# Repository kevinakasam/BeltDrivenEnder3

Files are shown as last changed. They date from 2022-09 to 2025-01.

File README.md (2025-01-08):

# BeltDrivenEnder3

### Versions/Variants
1: Stock V-Wheels        |  2: MGN-12H   |  3: Dual Z (Wheels and MGN)
:-------------------------:|:-------------------------:|:-------------------------:
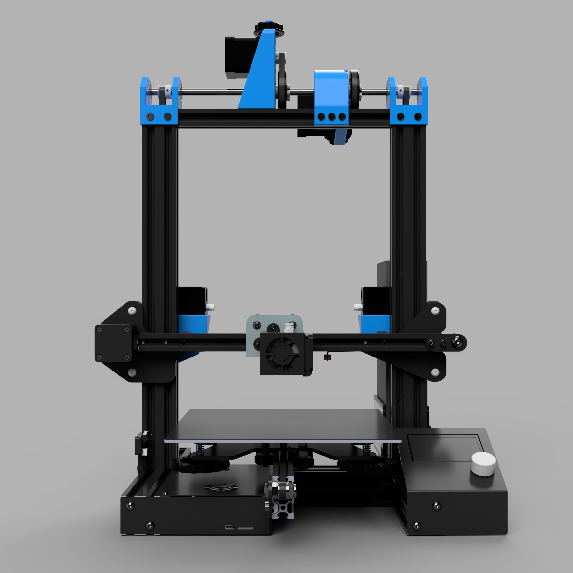
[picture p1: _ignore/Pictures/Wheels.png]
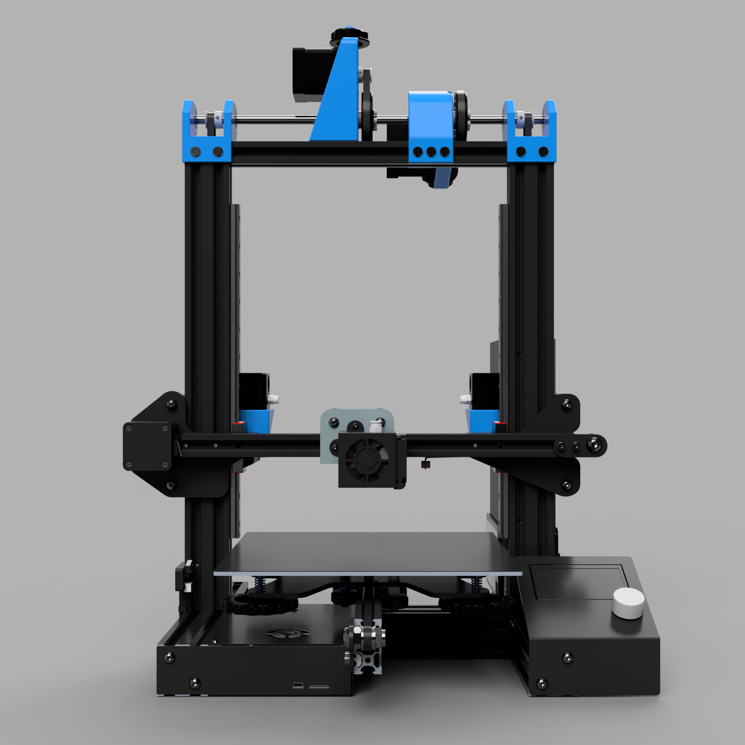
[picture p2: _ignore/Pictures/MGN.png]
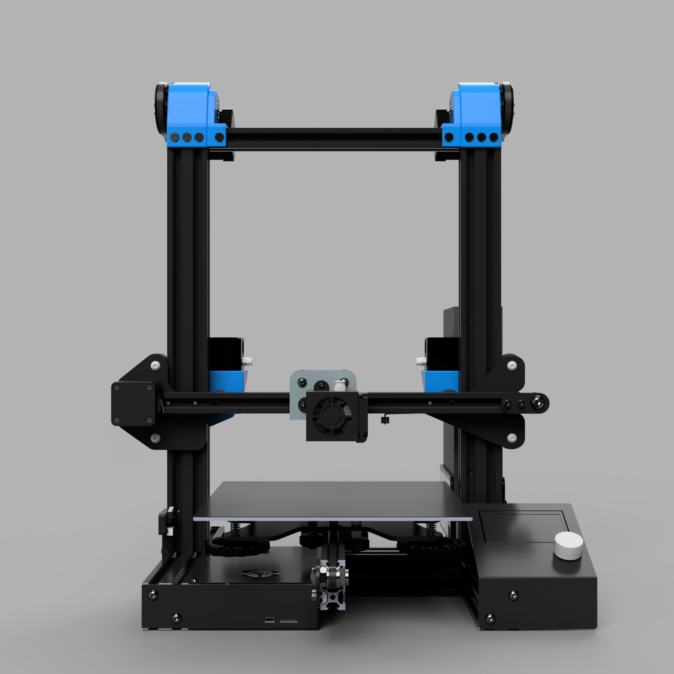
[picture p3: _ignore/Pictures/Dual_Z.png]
  |   |  

---
## Hello and welcome to the Belt Driven Z Mod.
### STLs, Bill of Materials and Instructions 
Please visit my [website](https://www.kevinakasam.com/belt-driven-ender-3/) to start the Config Finder. I have spent many hours creating a very interactive and easy to follow guide for the mod. You will get all the files you need at the end of the Config Finder, including a zip file with all the STLs, materials you need, and the instructions for your particular setup.

<a href="https://kevinakasam.com/belt-driven-ender-3/">
         Click
      </a>

### ❤️ Support my work

All my work is 100% Open-Source and free for everyone to use. But designing and developing all these mods takes a lot of time and effort, so if you appreciate my work and would like to support it and also help cover the costs of gettings the mods perfect, you can use one of the following links. Thanks a lot 🤍

<a href="https://www.buymeacoffee.com/kevinakasam" target="_blank">Buy Me A Coffee</a>


### Further notes
#### Versions vs. Variants
This mod now exists in the 3rd version (V3). The _ignore folder contains all the files for the old versions (V1 and V2). The current version (V3) exists in 3 variations:V-Wheels, MGN-12h and Dual Z (Dual Z works with both variants V-Wheels and MGN-12h). In addition, you can choose between the normal and ultralow version. I hope this clarifies the confusion between the versions and variants. Again please use the config finder on my [website](https://www.kevinakasam.com/belt-driven-ender-3/) to configure your individual setup.

#### Attention!
I'm not an expert and 3D printing is my hobby. So please be careful when you rebuild this mod and don't just go ahead. For my printer the parts fit perfectly.
Everybody bears the risks of a modification himself.
All parts can be modified as you like. :D

#### Print settings
All Parts can be printed without support. Keep the orientation for best results. Yes, you can use PLA but no, you shouldn’t use PLA. I used PETG for the unenclosured, ABS for the enclosured printer. Suggested print settings: 50% Infill, 5 Walls/Top-Bottom layer.
Good luck and happy printing!

#### Why I made the Mod:
My Ender 3 always had problems with the Z-axis, which were caused by a bent and misaligned leadscrew. Therefore I decided to convert the Ender to belts in Z as well.
This mod also solves the problem of a hanging x-axis on the right side. Because of the two belts, both sides run synchronously and can also be adjusted very precisely.

#### What this Mod can't do:
This mod can't solve problems that are caused by an inconsitent extrusion. Inconsitent extrusion means an untuned Flowrate/Extrusion multiplier and causes very inconsitent layers --> this looks like the picture below. To get rid of that you should tune all extrusion related values, like Flowrate an Linear Advance (Marlin) / Pressure Advance (Klipper). Take a look at this [tuning guide](https://ellis3dp.com/Print-Tuning-Guide/), its very well made (Works also for non Voron Printers and Marlin machines). 

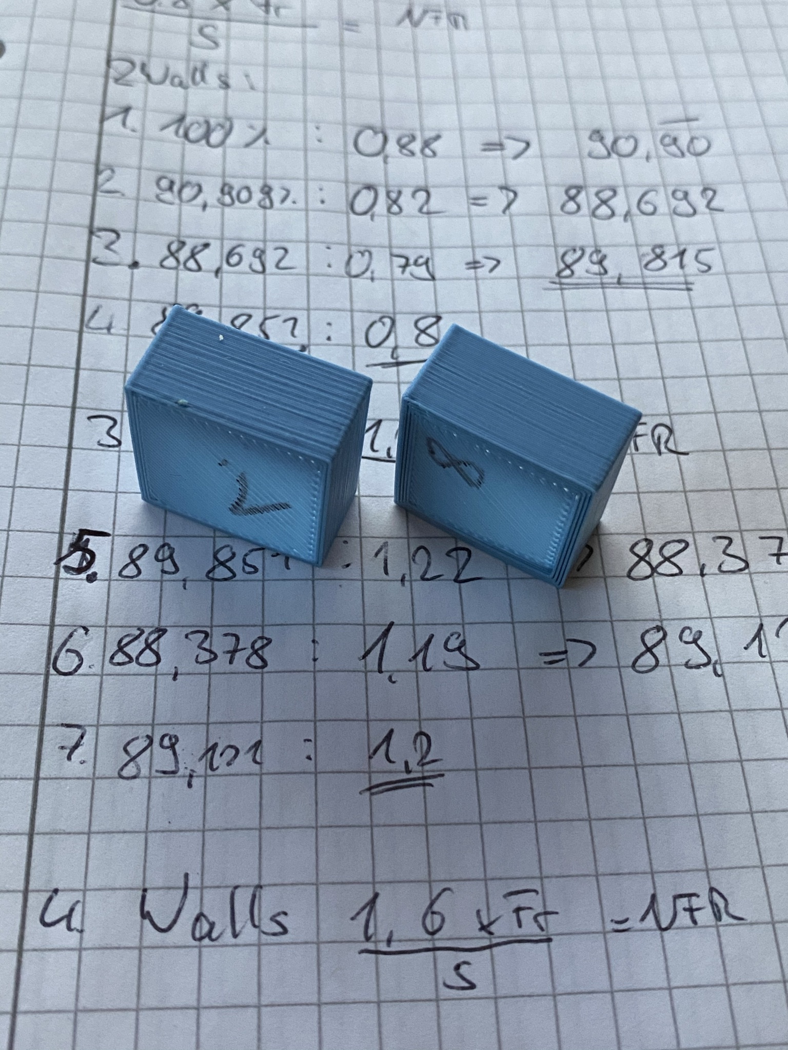
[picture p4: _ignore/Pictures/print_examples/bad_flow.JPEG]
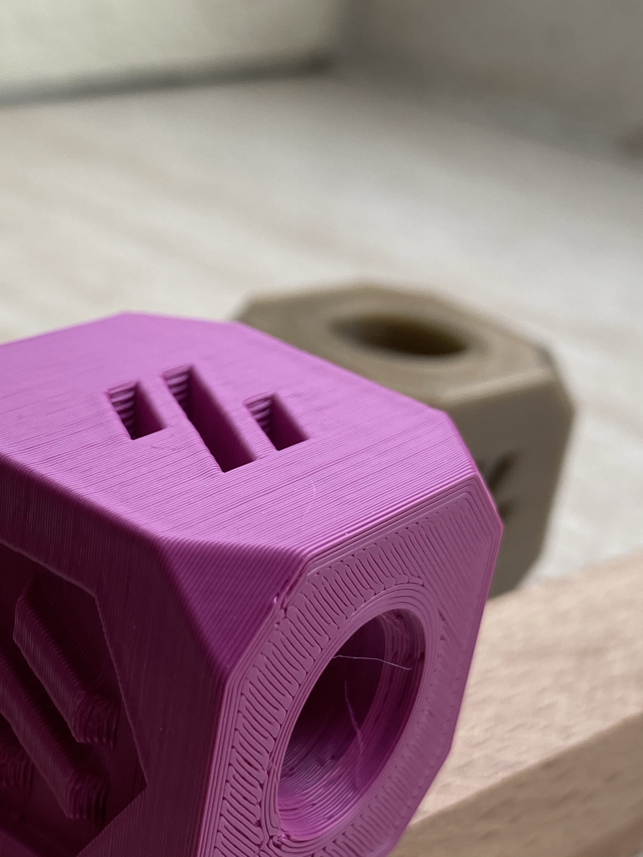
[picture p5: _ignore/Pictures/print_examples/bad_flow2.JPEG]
 

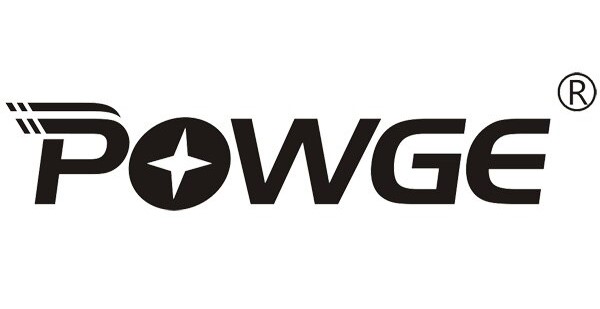
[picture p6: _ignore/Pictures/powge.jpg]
####  Powered by Powge! 
I am very very proud to announce that there is now a Motion Kit for this mod available for purchase! The Motion Kit from Powge provides all parts for Single Z or Dual Z, with F623 or 20T Idlers and in black or silver. This allows us to use high quality parts at a low price! Belts and pulleys match up perfectly and make the mod a little better. Thanks to Powge for this opportunity! (btw Aliexpress shows delivery times of several months, but shipping is significantly faster (to Germany it takes about 10 days)).
Link to the kit (also included in the BOM): https://www.aliexpress.com/item/1005003933709487.html

#### A word about *linear rails*.
There's a reason I haven't made a rail version in a very long time: Rails are not better than rollers in ***terms of quality***. At least the cheap rails you can buy on AliExpress. The tolerances are not good, they don't last long and can give z artifacts that you don't have with rollers. From time to time I get messages that the x axis drops as soon as the power is turned off. Every time that happens the mod uses rails. And like almost of those has cheap china rails. The problem with these cheap rails is that there is no friction at all, no tension and the Z axis is very poorly guided. The little Z motor has to carry all the weight because the rails are so loose they can't take any load. 
You also have to take care of the rails, lubricate and clean them from time to time, and make sure they don't leak. So you will spend a lot of money on a set of rails if you want good rails. Plus lubricants, cleaners, etc. Also, mounting the rails is more complicated. With wheels, you spent almost nothing on a new wheel, put it on, and you are good to go.
So I recommend trying wheels first and if you still want rails, you just need to print two small adapters to install the rails. Keep things simple ;)
  
#### How to use the toothed idlers
You have to remove the flage of the toothed idlers, otherwise they would get in contact with the profile.



### Acknowledgements
I would like to thank everyone who supported this project, especially *Guffy* and the *Awesome Helpers* from my Discord! 
Also a big thank you to my mate Deutherius who helped me with the initial setup of this mod!

#### Thank you Voron
This mod uses a modified transmission from the Voron 2.2. I made a different frame to mount it on the Ender 3. The tensionerarm and the tensionerring are from the Voron guys. These aren’t my work!!! The mount and the 80T gear are made by myself. Because the parts will be updated regularly, you can find the STLs I used on GitHub 

#### THANK YOU VERY MUCH!
I want to thank everyone who has helped me over the last months with feedback, support and confidence. Without you this mod would not have become sich a thing! Thanks also to Creality for the Golbal DIY Contest. I am very proud to announce that I could reach the 3rd place with his mod.

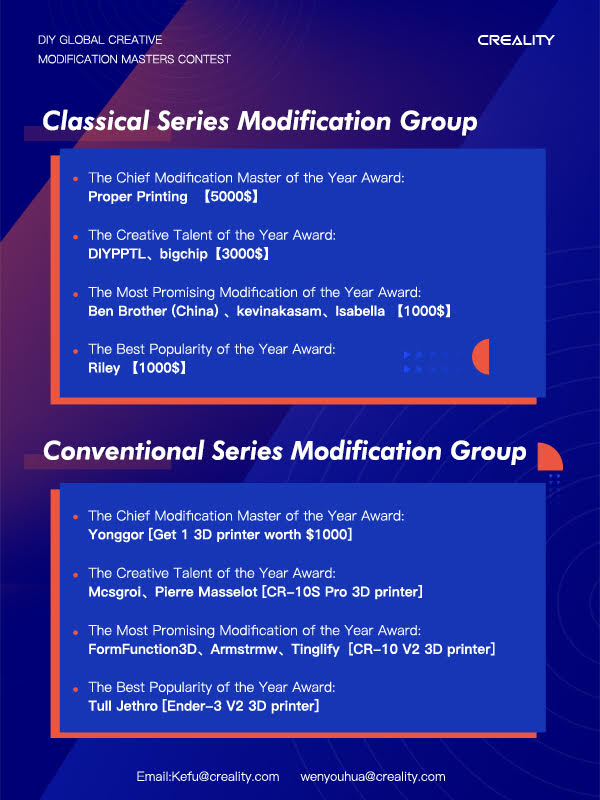
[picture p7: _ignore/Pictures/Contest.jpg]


## Print Showcase
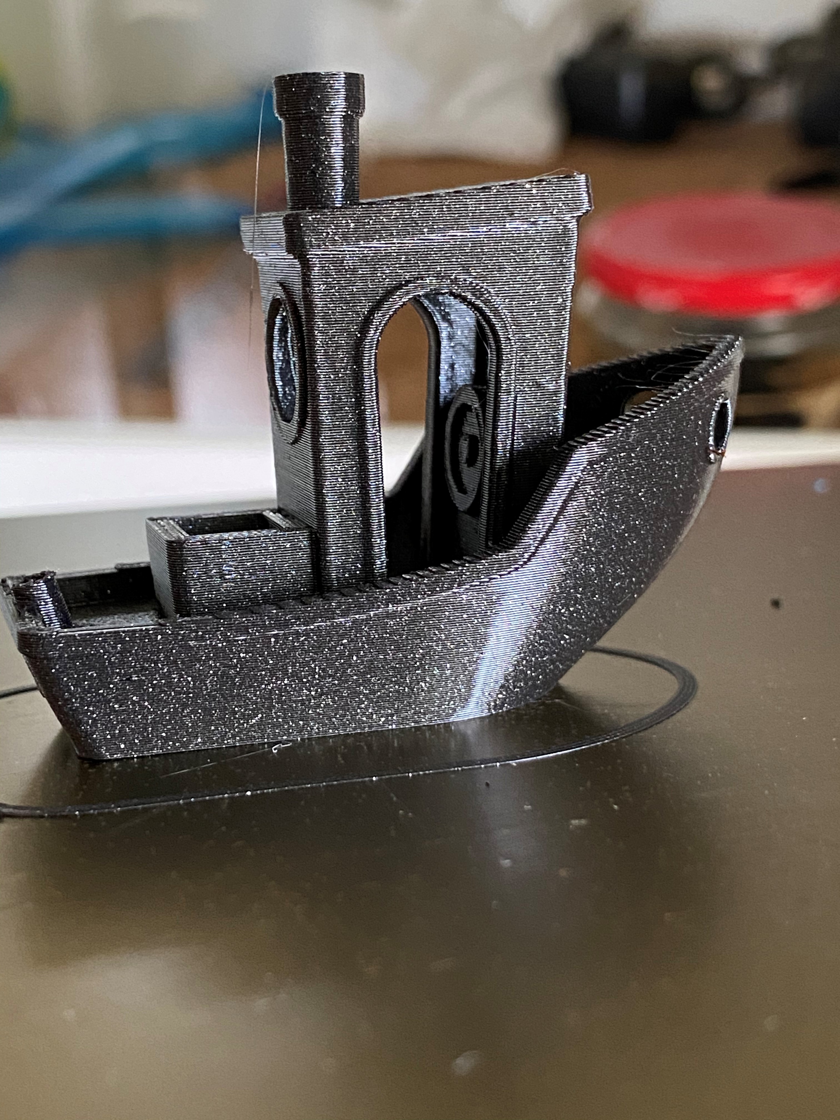
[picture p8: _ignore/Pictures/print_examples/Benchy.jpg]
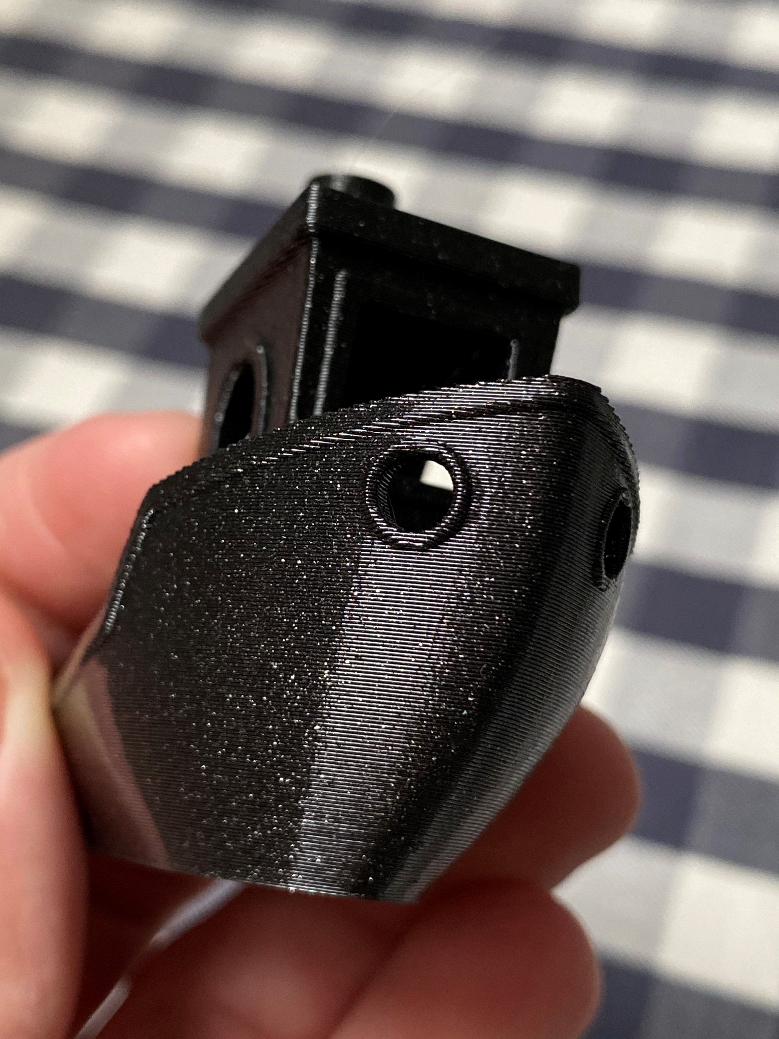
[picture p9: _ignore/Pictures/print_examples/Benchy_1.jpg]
 
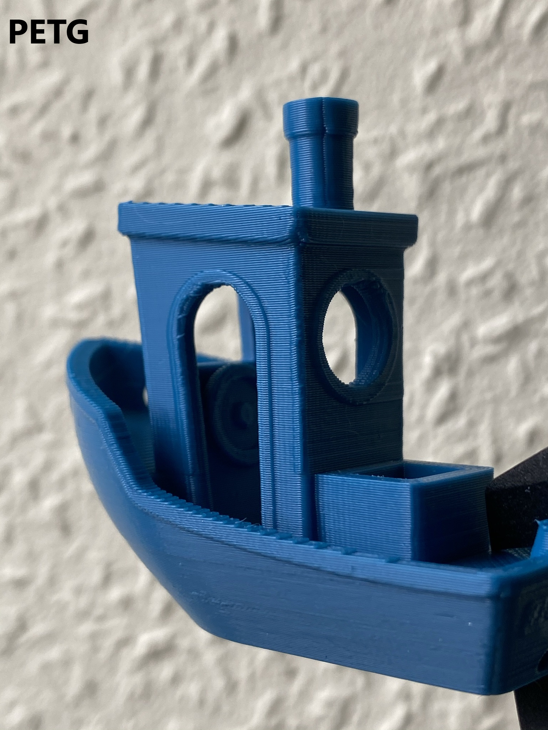
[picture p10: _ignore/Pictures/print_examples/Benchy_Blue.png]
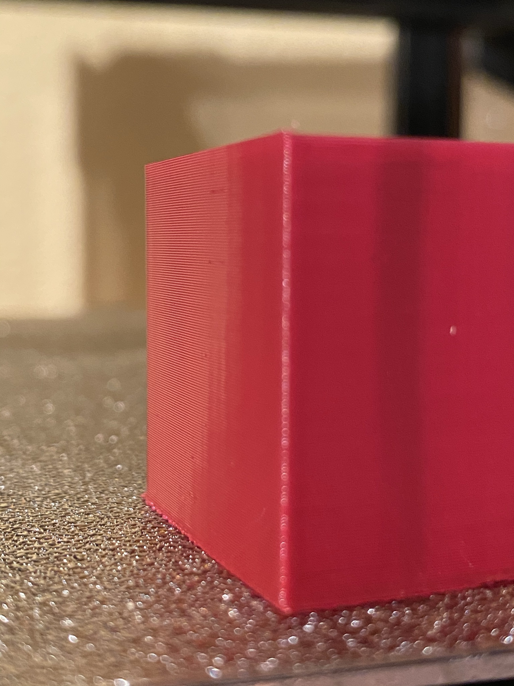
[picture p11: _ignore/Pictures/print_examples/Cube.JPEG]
 
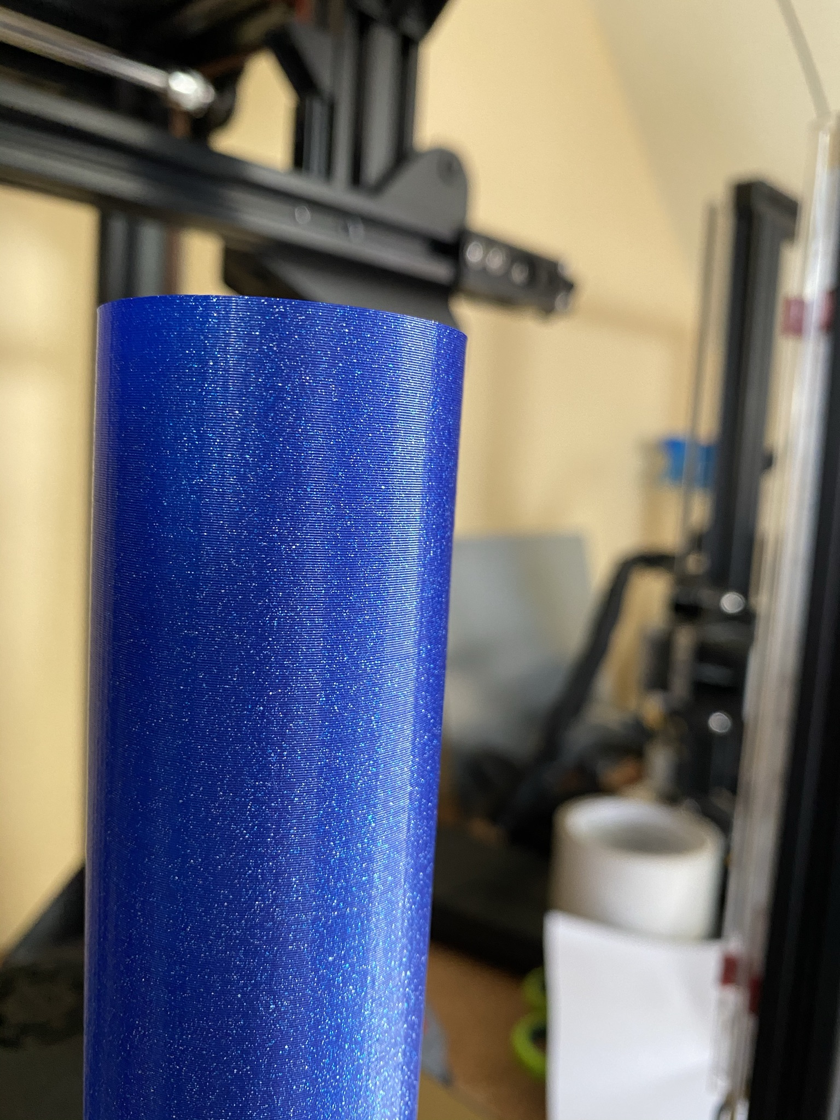
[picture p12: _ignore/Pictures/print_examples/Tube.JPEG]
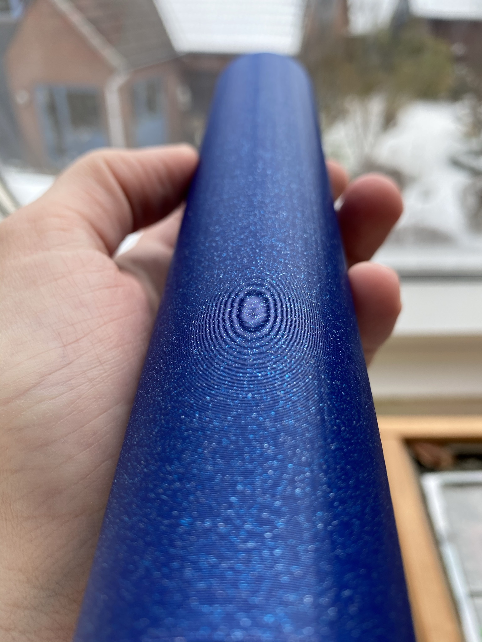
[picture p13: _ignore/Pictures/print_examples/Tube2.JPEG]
 

## Finally the video tutorials are finished!
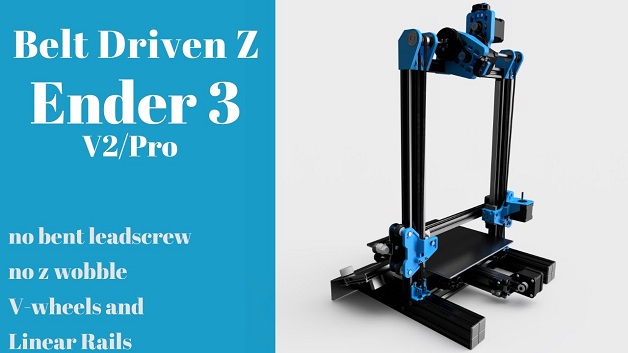
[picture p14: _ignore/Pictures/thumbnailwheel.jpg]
Video Tutorial (https://youtu.be/oUdoJUs8Zcg)


https://youtu.be/oUdoJUs8Zcg

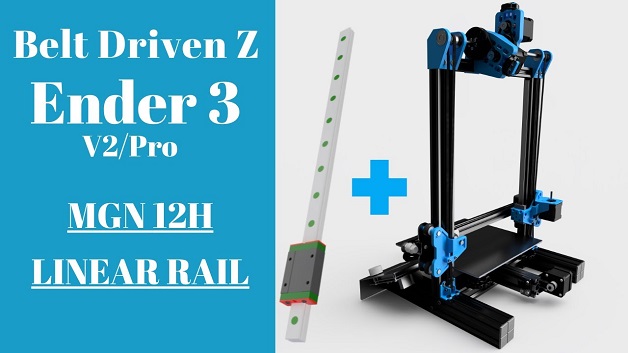
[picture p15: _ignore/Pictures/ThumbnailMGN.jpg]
Video Tutorial (https://youtu.be/bxTwFCPEIgg)


https://youtu.be/bxTwFCPEIgg

## Keybak
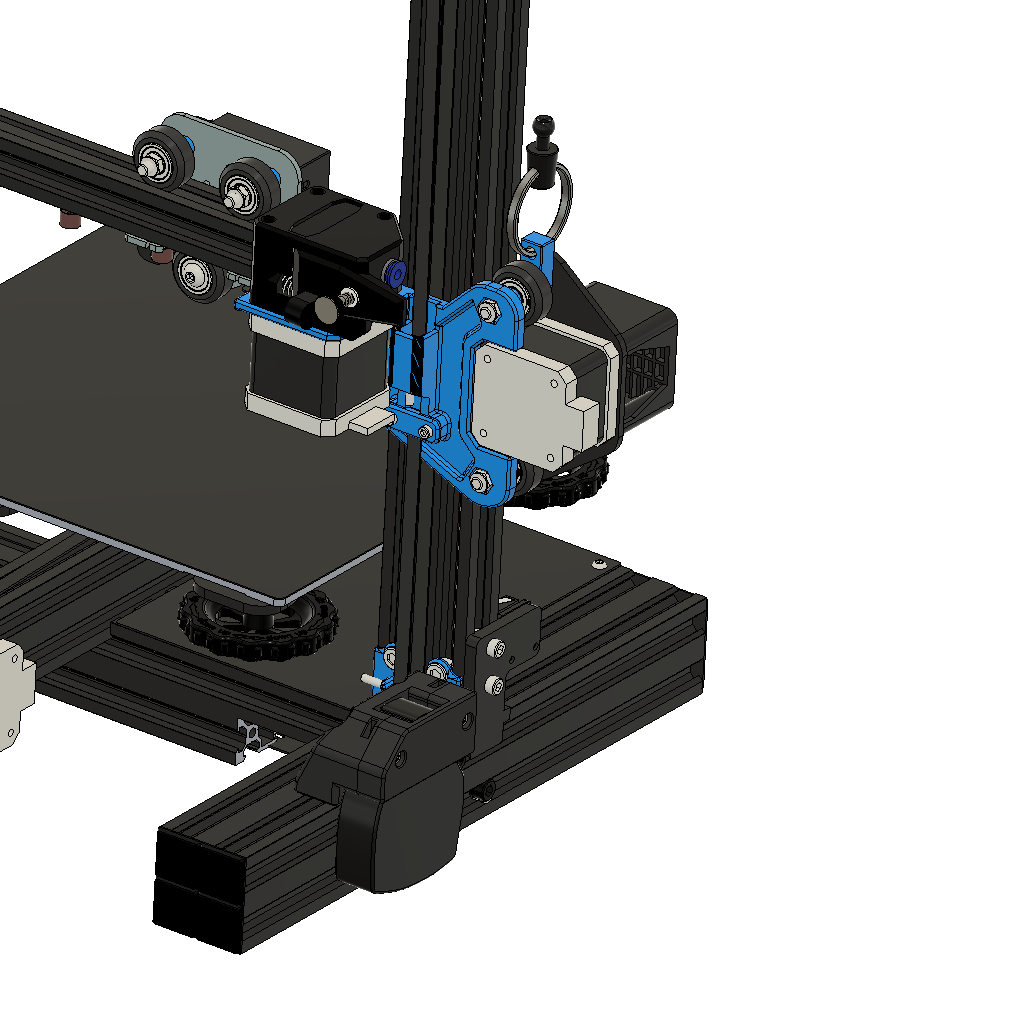
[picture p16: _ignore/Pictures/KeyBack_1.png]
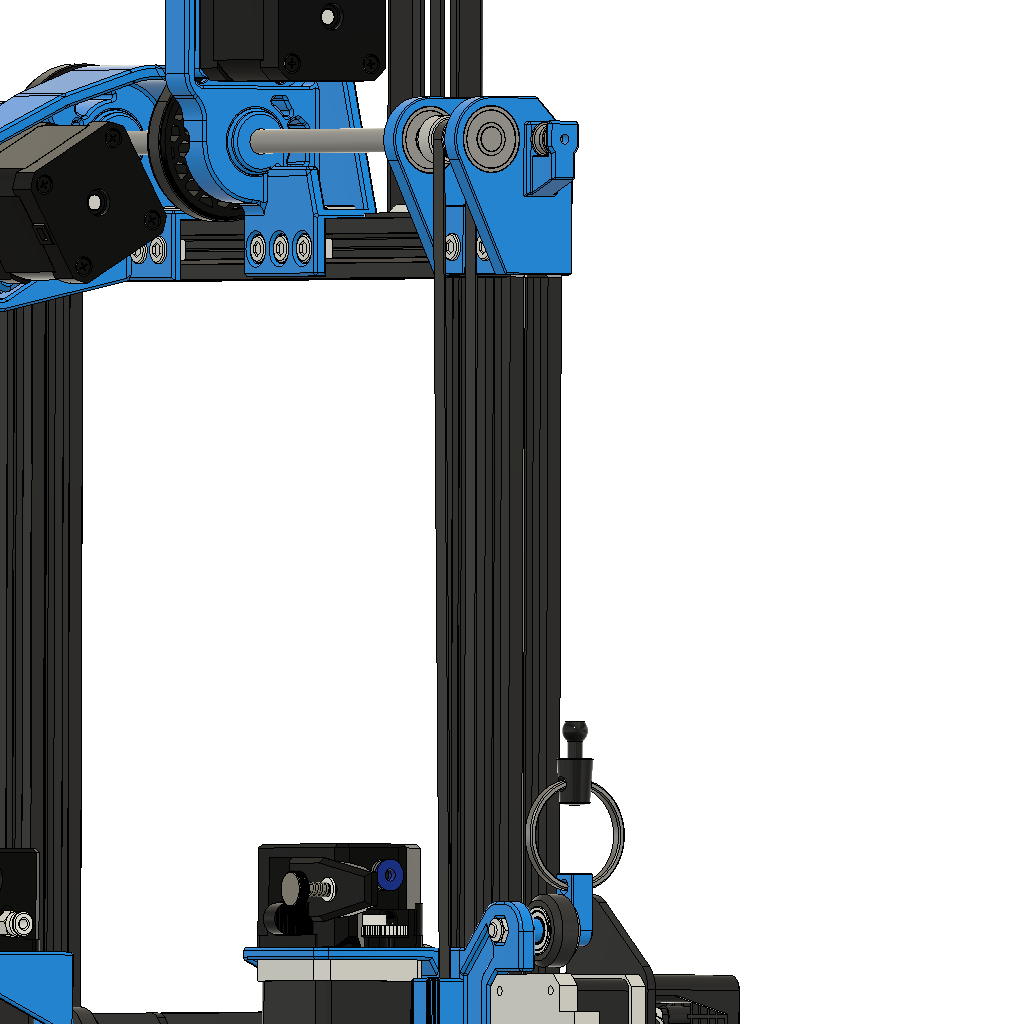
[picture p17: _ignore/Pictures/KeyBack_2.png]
 

Keybak system similar to the Switchwire design.
The files were remixed from the Switchwire CAD file.
For licensing reasons, all Keybak files are uploaded to GitHub only!
Idea from Voron team, thanks!

**Info: Because of the transmission it is not necessary to install a Keybak system.**
The 1:5 ratio increases the holding force of the motor so that it can hold the X axis up even when it is powered off.
A correctly adjusted belt tension is important for this.
If you are using the V-Wheels it is also important that they are installed correctly (See Troubleshooting).
From time to time I hear that users struggle to keep the axis up by using the belt tension only.
Therefore, I have designed the Keybak system. See BOM for all the parts you need.

What is a Keybak system and what is it for?
A Keybak is actually used to secure keys to a wire rope.
Depending on the Keybak, they can support a lot of weight without the cord extending on its own.
The Keybak used here is strong enough to support the x axis. It takes the load off the motor and shares the weight of the axis with it.
__It is still important to tension the belts properly!
If the belts are not tightened enough, there will be unclean prints later!__
So make sure that the Keybak doesn't mislead you into not tightening the belts enough.
See my FAQ video on how to properly tension the belts (video coming soon).

You will have to print a new 1_LeftTop_A and a 3_spacer to use the Keybak.

## FAQ 
### Do I need to change the firmware?
NO! You do not have to change anything in the firmware. This modification works with the stock board and stock firmware.

### Can I use PLA to print the parts?
Yes and no. All parts should work with PLA, except the motor tensioner arm. The motor has to hold more weight now, so the motor could get warm. Since PLA deforms at ~40°C you should keep an eye on your motor (see troubleshooting). Because of that I would recommend PETG. When you're printing inside an enclosure you should use ABS. Try Esun ABS+, super easy to print, and much stronger than PETG.

### Is this mod also compatible with the Ender 3 V2/Pro etc?
YES! You can use this mod with all Ender 3 versions.

### Can use this for my Creality CR printer?
View the makes on Thingiverse. Some of you made a CR build so I thing it should fit. Feel free to give some feedback about that.

### Do I need a hardened steelrod?
NO! A cheap aluminium or "normal" steelrod is just fine. There's also a transmission (rotated and unrotated) that hold a bearing inside, so you have some extra support in the middle of your rod. You also could use your leadscrew to minimize the costs.

### Dual Z? G34?
So you want to use two stepper motors to have an indipendent z axis? Thats possible of course! Just use the files from the Dual Z folder! See BOM for detailed parts list.

### I have a special question/ I need a custom version but I'm new to CAD. Can you help me?
Yes of course! I'm happy to help, so please contact me via Discord (kevinakasam#2097). I'm sure we will find a solution for your problem :)

### Can I support your work?
Thank you very much if you want to support my work! But please dont feel obligated to do so. All parts are free and open source and will stay that way! If you still want to support me, you can find a donation link at the bottom of this page. Really many many thanks! :)

## Troubleshooting
### My Z motor moves in the wrong direction!
Thats a quick fix. Just remove all the pins in you motor connector that goes into the mainboard (like I showed you in my video) and insert them in the opposite order (4321 instead of 1234).

### My Z motor gets super hot!
First of all: A warm or slighty hot motor isn't a super bad thing. But you should change that. Try to lower your V-ref/Amps till the motor stays hand warm. But be careful to not reduce the current too much, or your motor will lose steps. The stock Z motor is very small so it's a big job for the tiny motor. Don't worry if your motor gets warm.

### My z axis drops as soon as power off my printer!
Probably the most asked question, but I can promise that your axis does not have to drop! As already mentioned, the z motor is very small. Therefore the magnetic field that exists in the motor even without power isn't very strong. But it's strong enough to keep the axis up.
#### I don't care, my axis is dropping, what can I do?
1. You are using the original V-Rollers? Be sure they are properly set up. Turn the eccentric nut until the rollers are in contact with the profile. Put a little tension on the rollers, but not too much! Do not risk a flat spot of your rollers. The tension is correct when they are tight, and you can't turn them with your finger in the same place, but the axis moves when you turn the rollers.
2. You have no rollers or your axis is still dropping? Tension your long belts a little more. Increase the tension until your axis stops dropping. Be careful not to break something. But the parts can take a lot of tension. Otherwise, check out my FAQ video about how to tension the belts (THE VIDEO HAS STILL TO BE CREATED).
3. Tension the small looped belt a bit more as well. But very carefully! Usually the tension only needs to be high enough to keep the belt from slipping over the printed wheel. But you can increase the tension a little bit. But not too much, otherwise the motor can't turn anymore.
4. That sounds too complicated? Your motor is also too hot? A solution would be a bigger motor, like the one on the X and Y axis. A bigger motor is able to hold the axis up very easily, with less tension and less heat. But as I said, this is not necessary, it also works with the original motor.
5. New solution: Install the Keybak System (added 31.10.2021).

---
### Changelog:
25.02.2023: Update? It's been a while! Release of the **V3.7** files.
- Plate update
	-The right plate got an extra hole to access the M4 screw that holds the metal plate to the X axis.
	- The holes for the hex nut got a bridging pattern so no more filament can curl there.
- Transmission Update
	- All the transmission bodies got a cutout to make it easier to tighten the motor shaft grub screw.
	- Utralow and Dual Z transmissions have also received a hole to access the 20T pulley grub screws.
- Update of the lower parts
	- The small hill that holds the 3x14mm pin in place is now much smaller and it should be much easier to insert the pins
- V3_Extras update
	- Added a version with heat inserts that replaces the M3 hex nuts with heat inserts.
	- MGN 12C support
	- Printer adaptations for Artillery Hornet and Tevo Tarantula Pro

21.09.2022: Release of the Website and the new instructions!

23.08.2022: Big Update! Release of the **V3.6** files. 
- Almost all Parts got an update:
	- Housing for the tensioner on the plates is thicker now
	- Bottom Parts use Pins now instead of  M3 screws (old files still available in `\V3\_old_V3_parts` in case you want to use screws)
	- Replaced printed thread on the transmission tensioner with a M5 Screw
	- EOL for unrotated and non-exttra bearing transmission 
	- Revomed the top holes from the transmissions and Top part --> less hardware needed and it was a pain to install these, sorry for that!)
	- The UltraLow version is now an "official" variattion of this mod (no longer in the V3_extras folder). 
- Things that will follow:
	- New Instructions with an updated BOM --> Interactive with a ton of information

14.07.2022: Added MGN 9H support in the V3_Extras folder.

09.05.2022: Updated the BOM. (16T link was wrong, sorry for that!)

27.01.2022: Updated the BOM.

19.01.2022: Small Changes
- Added the V3_Extra folder to store the customizations I made for you.
- Added the small hole in the V3.5 plates again for the belt from the tensioner block.

09.01.2022: Second big Update: **V3.5**
- Adjusted the Belt path so they're parallel now. This was requested quite often, sorry it took so long.
- Added a version for toothed bearings. 
- Added Dual Z Version.
- Removed upper holes in the Top parts, so you do not have to unscrew the top profile.

31.10.2021: Big Update!
- Moved the extruder to the stock position for the V3.4_Bowden plates (Fits BMG now too). Idea from trohnjavolta, thanks!
- Split the tops into two parts to make them easier to print and more stable (Top_A and Top_B). Idea from sztywniutko (Thing:4911634), thanks!
- Added a PSU mount.
- Added a Keybak system similar to the Switchwire design. The files were remixed from the Switchwire CAD file. For licensing reasons, all Keybak files are uploaded to GitHub only! Idea from Voron team, thanks!

17.08.2021: Made some small tolerance changes to the rotated transmission and the inner M3 parts.

31.07.2021: I made a mistake and uploaded the wrong files for "LeftTop" and RightTop". If you downloaded the files from Thingiverse between 15.06.2021 and 31.07.2021, please download the latest version. I am very sorry! Thanks to mbarryton for the hint!

15.06.2021: **Important!!!** Both Versions (rotated and unrotated) are compatible now. Both versions now have the identical LeftTop and RightTop (the one from the rotated version).

15.06.2021: I have added a version of both transmissions that include a ball bearing. So the rod is supported in the middle by another ball bearing.

15.06.2020:  Updated CAD with all Versions. Many thanks to Regulus who did a great job adding many wonderful details to the CAD file. All parts are now properly aligned, all fasteners are added and named. Seriously many many thanks!

02.06.2021: Added Left and Right V3.3. Changed the design of the lower clamp profile. If youre using the 3.1 or 3.2 that's totally fine;)

02.06.2021: Updated the 80T Gear on GitHub. reduced the outer diameter a bit so theres a bigger gap to the profile. Thanks to Regulus!

06.05.2021: Modified MGN Version fits now for Ender 3 (Pro) and Ender 3 V2. Bowden Version tested. Thanks to Jon!

04.05.2021: Added a Video Tutorial.

02.05.2021: Added Left and Right V3.2. Tensioner were missaligned by ~0.5mm. Thanks to Zardozer for the hint! If youre using the old V3.1 its totally fine. I'm using them as well:D

14.02.2021: Changes for the MGN Version!! LeftV1 added. Please print 1_Left and 1_LeftV1. I would appreciate feedback for Left or LeftV1. I have created the files with the official CAD, but the M4 screws differ in the position by 2mm. Please print both versions and tell me which fits, thanks:)

26.02.2021: Added Bowdenversion.

26.02.2021: Started Changelog.

--- 
Donation Link: https://www.buymeacoffee.com/kevinakasam or via [Paypal](https://paypal.me/donationskevinakasam?)

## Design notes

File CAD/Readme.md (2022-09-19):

All supported Step and Fusion 360 files.

### Original file link:

Ender 3 Step: https://github.com/Creality3DPrinting/Ender-3/tree/master/Ender-3%20Mechanical

Vron Transmission Step: https://github.com/VoronDesign/Voron-2/tree/Voron2.4/CAD

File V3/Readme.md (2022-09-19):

# New V3.6 Parts!

With the V3.6 Update I changed the structure of the folders as well. In this main folder are the common files for all variation of this mod (Z-Plates, Bottom Parts, etc.). You will find all other parts in the corresponding folders.

Note:
- With the V3.6 update you need **two additional M5 nuts** and **one M5x30mm screw** per transmission (so **Dual Z will need twice as much**) and two 3x14mm pins for the new bottom parts (pins are already included in the Powge Kit. You can use the old bottom parts with a M3 screw in the `\V3\_old_V3_parts` folder). Please forgive this extra note, I will update the bom with the new instructions!
- You have to choose between Bottom_20T and Bottom_F623, depending on what you want to use (send `?f623vs20t`on my discord in the #belt-help channel to get a small description about that)
- Dual Z and UltraLow are now also contained in this folder
- MGN: If you want to use MGN, the files are still the same in the V3_MGN folder. You will need these parts in addition.

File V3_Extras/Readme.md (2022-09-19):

I get a lot of requests to customize my mod.
In the future I will make them available here. I will add a small description to each extra, but there will be no bom, instructions or updates for these files.
Maybe there is someone who was looking for exactly this customization :D

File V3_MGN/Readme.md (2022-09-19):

All Files from normal V3 needed, except the spacers.

All Files are tested.

I have uploaded a distance bracket to make it easier to attach the rails.

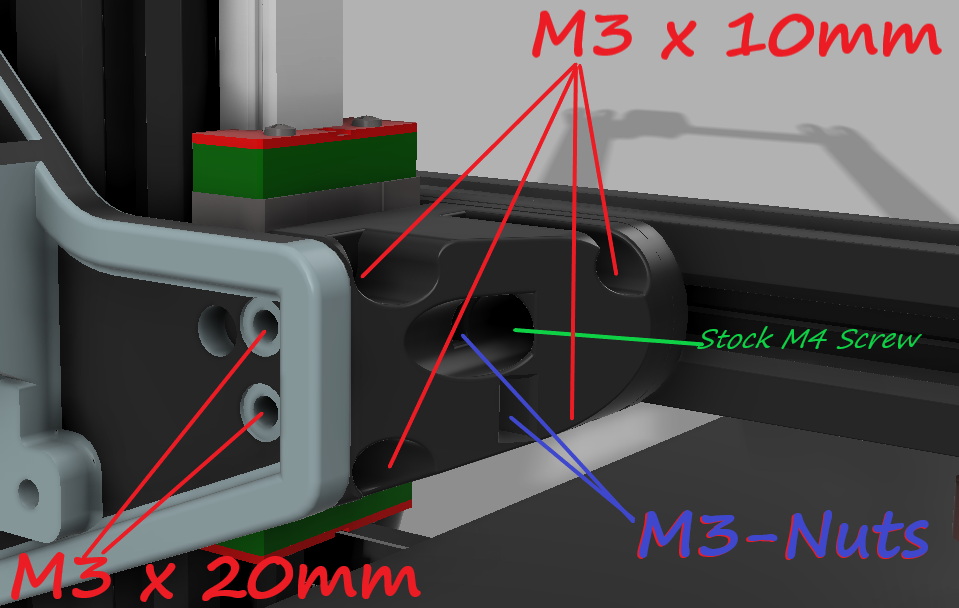
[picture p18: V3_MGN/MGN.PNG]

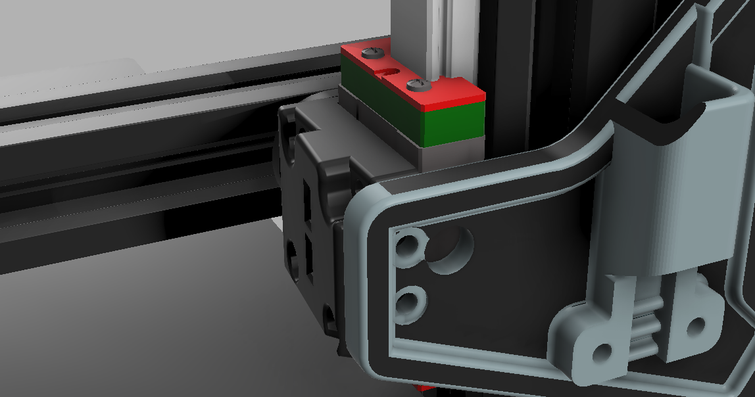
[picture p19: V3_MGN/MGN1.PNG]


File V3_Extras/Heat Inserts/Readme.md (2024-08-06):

Thanks to Hr_Raven for the idea and testing!

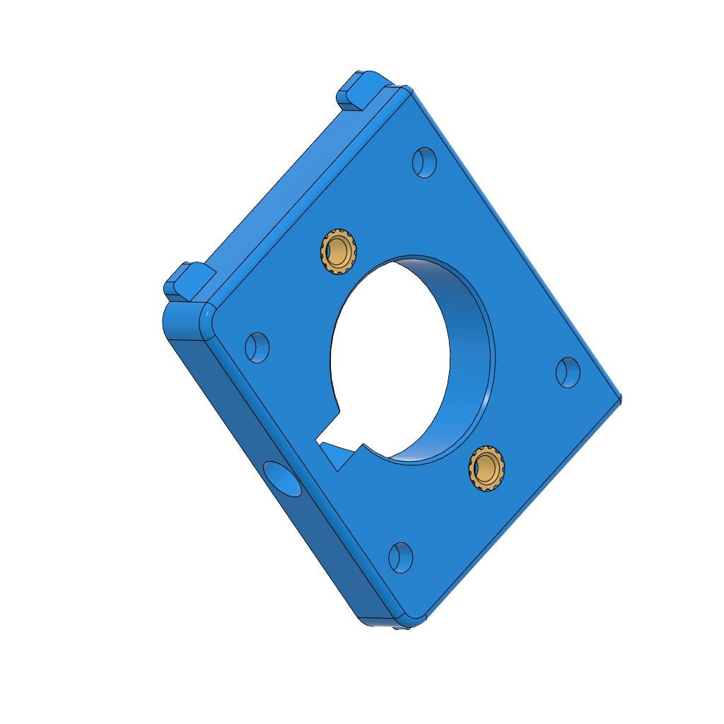
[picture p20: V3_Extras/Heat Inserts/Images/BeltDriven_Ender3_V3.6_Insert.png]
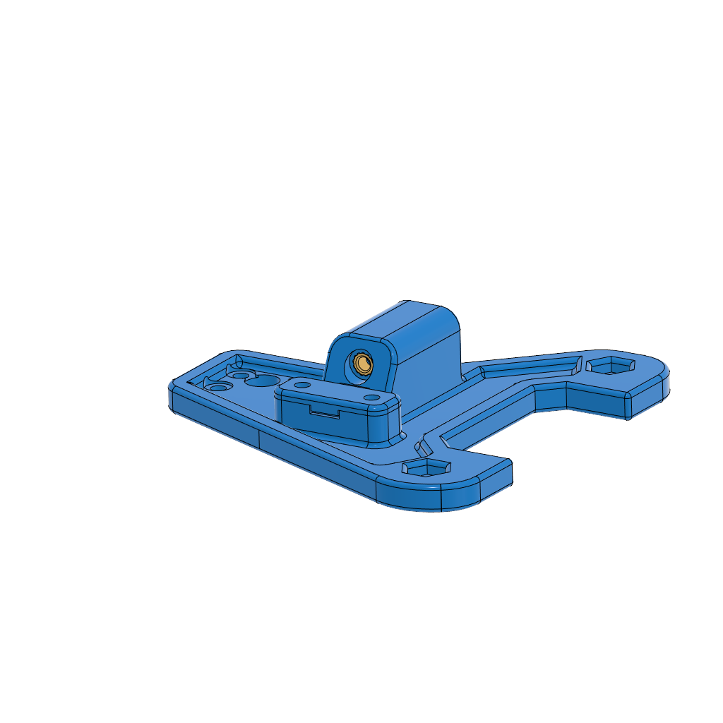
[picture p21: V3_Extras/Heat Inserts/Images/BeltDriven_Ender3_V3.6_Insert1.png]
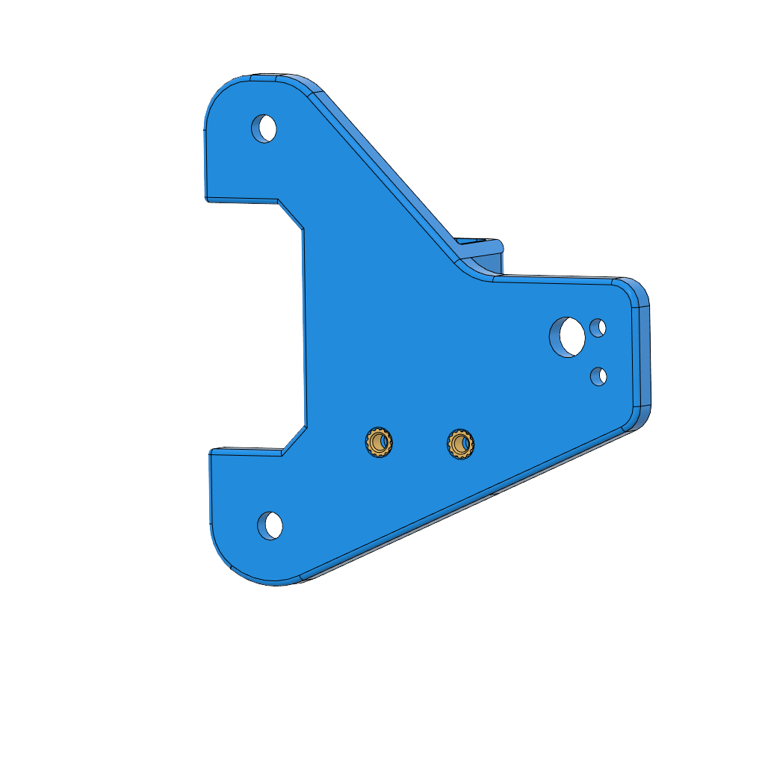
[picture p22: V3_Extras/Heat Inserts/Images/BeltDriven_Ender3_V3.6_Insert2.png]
  

This version replaces the hexnuts with heat inserts (the standard Voron M3x5x4 ones) on the plates and on the motor tensioner arm.

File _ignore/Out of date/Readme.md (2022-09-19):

Files for the V1 and V2 of this mod. V3 is most current version for all Ender 3 styled printers.

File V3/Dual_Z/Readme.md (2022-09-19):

Files for the Dual Z Version. The files are slightly modified from the V3 files. With this version, the transmission sits on the outside (see photo below). This allows you to use the metal 80T pulley as well as larger gears than 80T to increase the z-axis resolution.
Instead of one long, you now need two 65mm rods. Besides a second motor, all other transmission parts are needed twice. Check BOM for a detailed parts list.

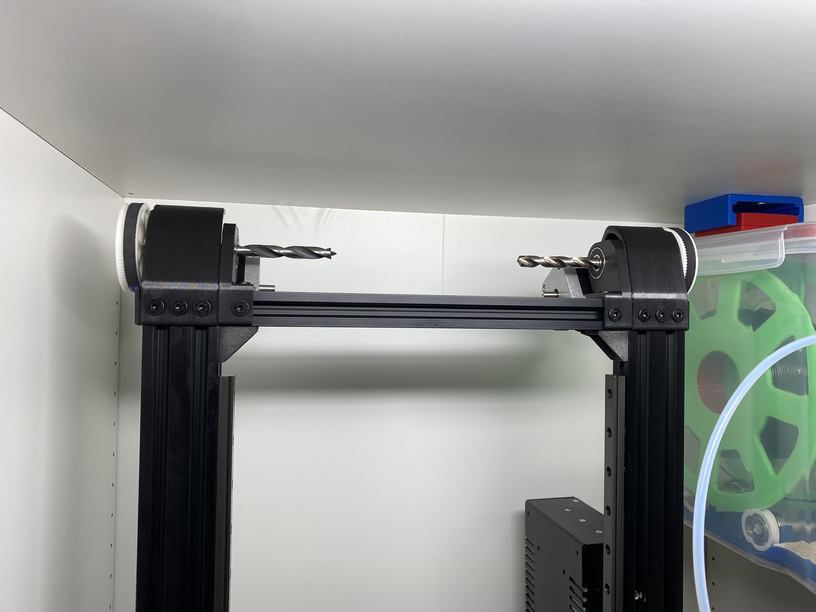
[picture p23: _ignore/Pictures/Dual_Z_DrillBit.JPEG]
 

Dual Z can also be used with the normal V3 files, but the transmission would be on the inside (see CAD photo blow). Therefore the inner top part is replaced by the (mirrored) transmission.

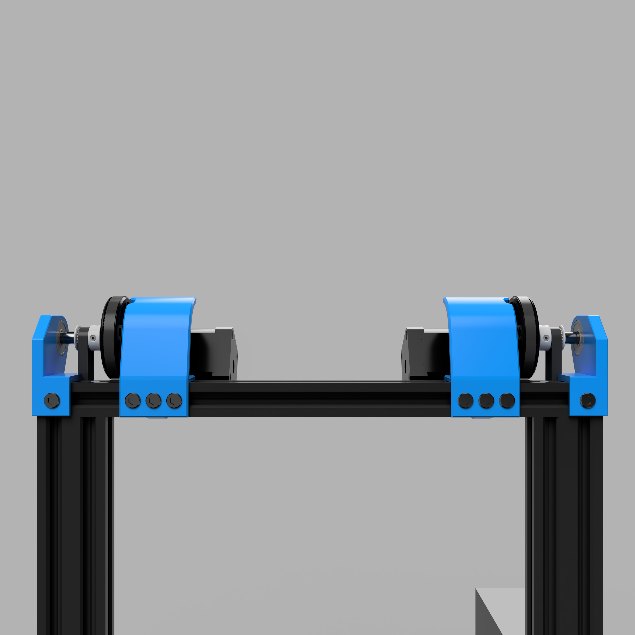
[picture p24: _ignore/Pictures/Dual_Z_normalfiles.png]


If the motors can be controlled independently (two drivers on the board, not both on the same driver), G34 can be used. If both motors cannot be controlled separately, G34 will not work and Tram Z must be used instead (as with Prusa Mk2s/Mk3s). Your Board needs UART driver for this. For all Klipper users I have written a macro that can be used:
```
Tram Z Makro for Klipper:

[force_move]
enable_force_move: TRUE

[gcode_macro Tram_Z]
gcode:
    G28
    G1 X125 F6000
    G1 Z230 F1000
    SET_TMC_CURRENT STEPPER=stepper_z CURRENT={0.3} # Makes the weak and movements will perform with less power so mothing brakes.
    FORCE_MOVE STEPPER=stepper_z DISTANCE={15} VELOCITY={5} ACCEL={5} # The motor will make some noise when it touches the top beam. Adjust the z travel if possible/needed.
    SET_TMC_CURRENT STEPPER=stepper_z CURRENT={1.0} # Set this to your normal default z run_current.
    G28 Z
```
A demonstration of the macro can be seen on Youtube:

https://youtu.be/GGOv1CKP1a4

The macro should be done whenever the axis is moved by hand (this also includes the X axis when the power is off, the axis may moved).

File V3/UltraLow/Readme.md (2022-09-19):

With this parts you can use the Belt Driven Ender 3 in your Lack enclosure. It adds just a height of 38mm, there's no way to get it lower without changing the belt path.
For single Z the BOM is still the same, but you will need a longer rod (e.g. the leadscrew) because the transmission is mounted on the side.
For dual Z its also the same. 

### Versions
1: Single Z        |  2: Dual Z   
:-------------------------:|:-------------------------:
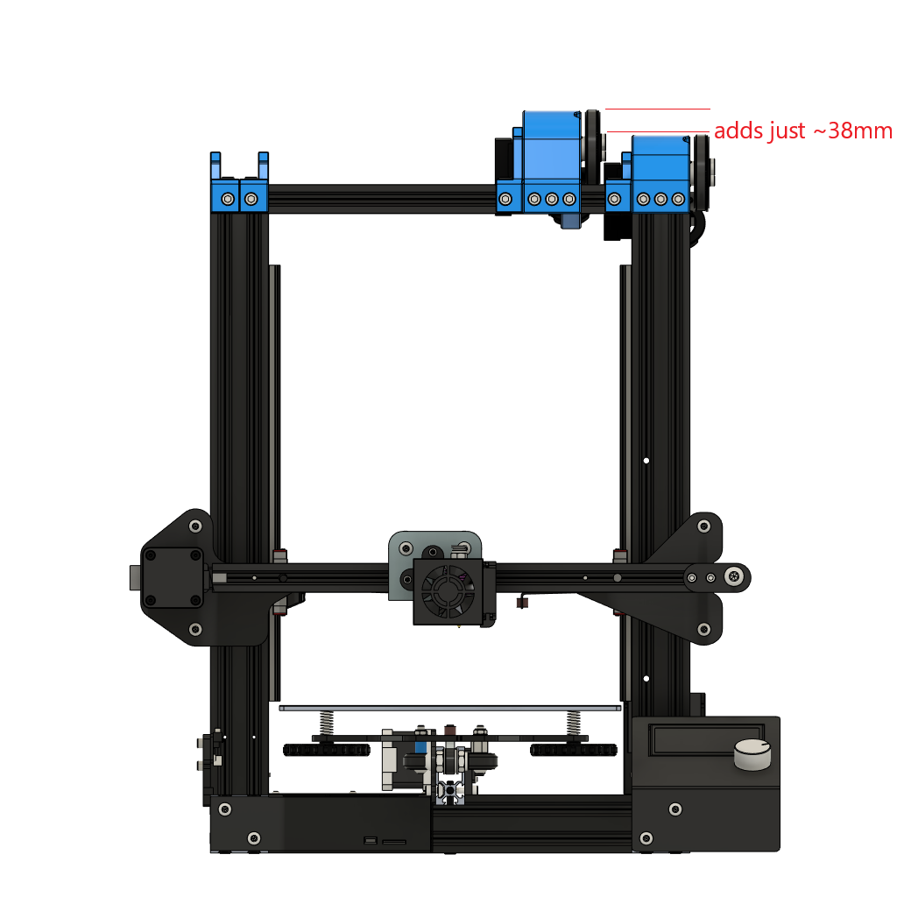
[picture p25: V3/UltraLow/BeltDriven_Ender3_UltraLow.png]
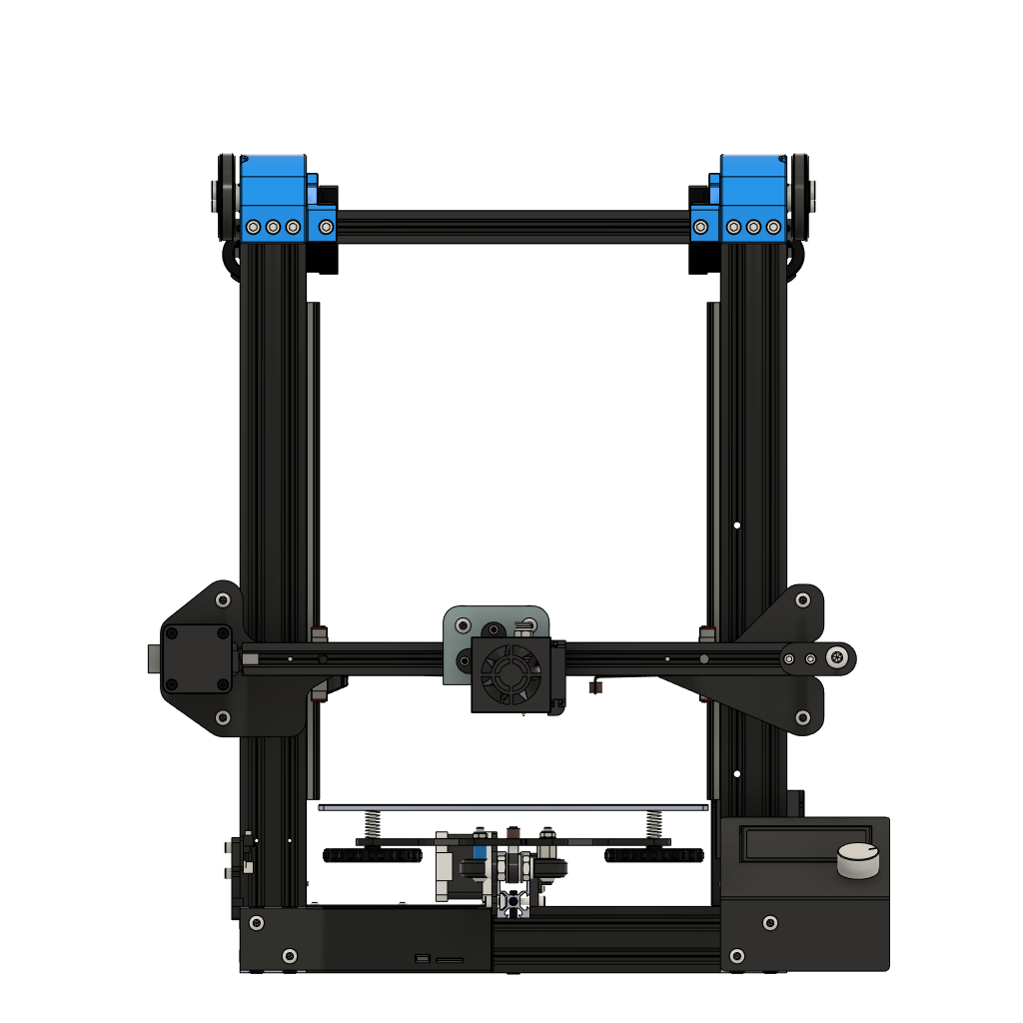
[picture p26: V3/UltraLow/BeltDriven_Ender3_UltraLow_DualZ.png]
  |

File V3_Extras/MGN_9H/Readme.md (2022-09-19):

# V3 MGN 9H Version
Currently untested. Requested by EVAC.

Adaption of the V3_MGN files so you can use MGN 9H instead of MGN 12H.

All other Hardware stays the same. Spacers are also identical to the MGN12H version. I just copied them here to have all files combined. 

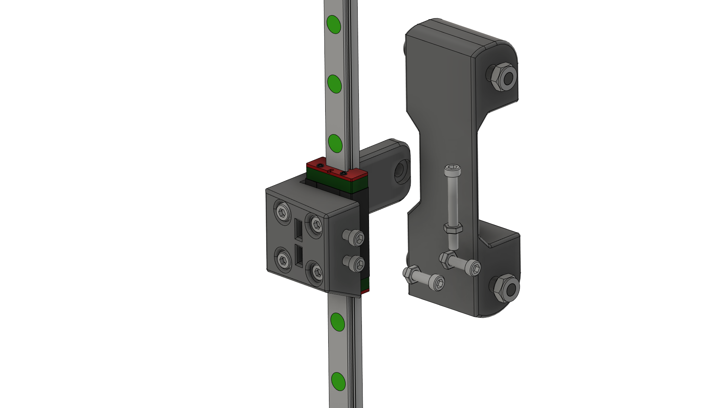
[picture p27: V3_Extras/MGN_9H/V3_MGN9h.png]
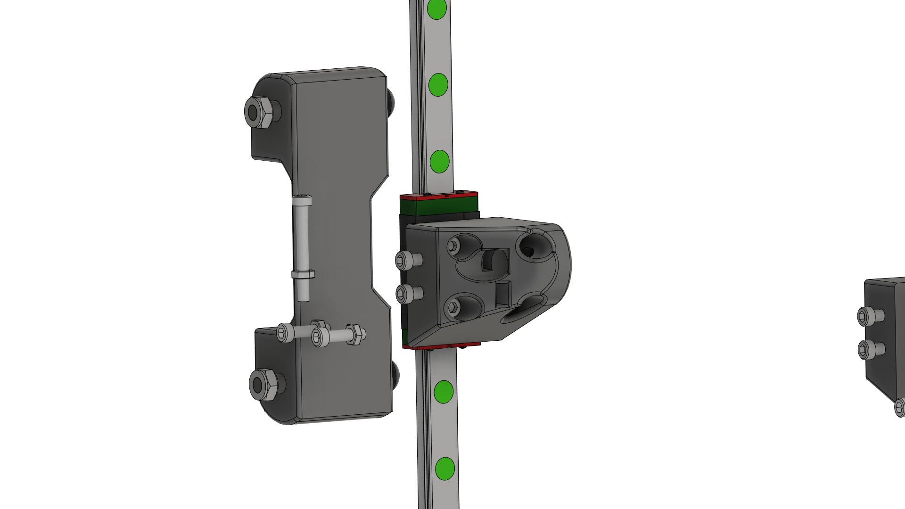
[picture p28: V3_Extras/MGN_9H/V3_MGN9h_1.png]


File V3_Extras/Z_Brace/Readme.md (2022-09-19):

Just a small adaption to the top parts to use a z brace mod (https://www.thingiverse.com/thing:4533346)

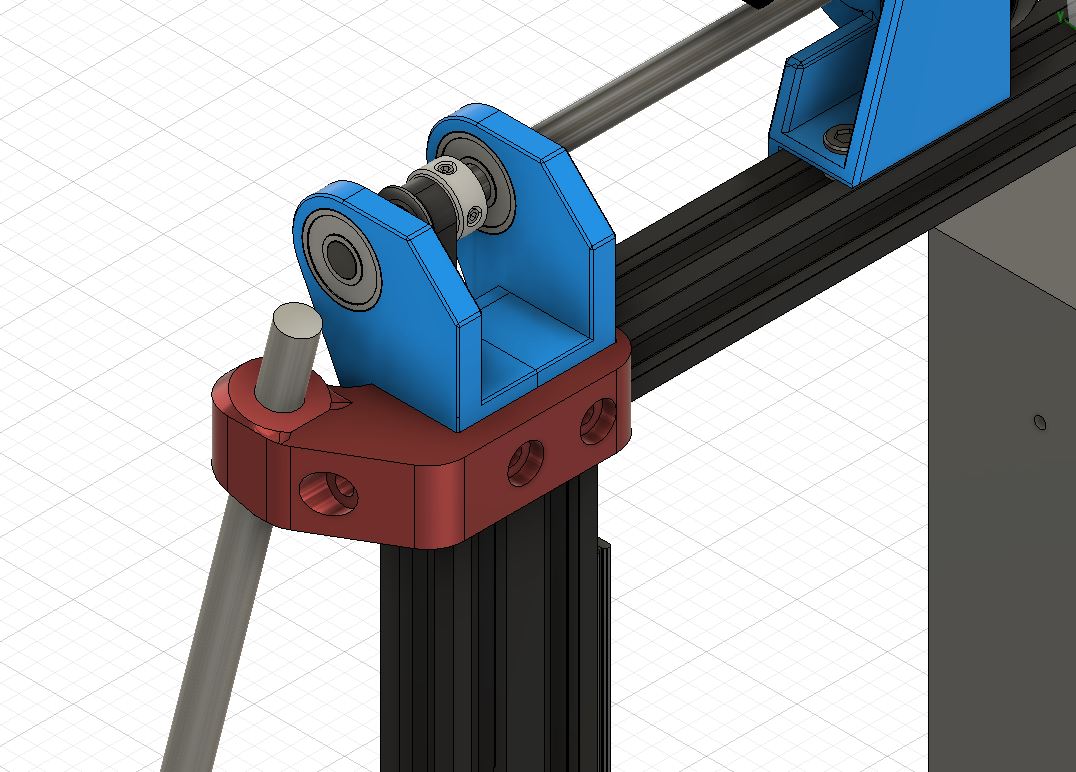
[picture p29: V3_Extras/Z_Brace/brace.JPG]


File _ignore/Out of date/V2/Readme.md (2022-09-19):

All files for the V2 version, you should use the V3.

Info for V2: with Voron Transmission

***English version below***

Achtung!
Ich bin kein Profi und betreibe 3D-Druck als mein Hobby. Also bitte überlegt selbst, wenn ihr euren Drucker umbaut und legt nicht einfach los. Für meinen Drucker passen die Teile hervorrangend. Die Drucke sehen wirklich perfekt aus.
Jeder trägt die Risiken eines Umbaus selbst.
Alle Teile können nach Belieben verändert werden. 

Upadte V2:
Im Gegensatz zur Version V1 könnt ihr diesesmal alle Teile vom Drucker wiederverwenden. Somit ist der Umbau einfacher, stabiler und günstiger. Selbst die Pulleys könntet ihr drucken und somit Geld sparem, würde ich jedoch nicht empfelen.
Die angebrachte Übersetzung ist die größte Neuerung. Dadurch erhöht ihr nicht nur eure Auflösung in Z, auch sinkt die X Achse nicht mehr 0, sobald diese keinen Strom mehr haben (entweder nach dem Druck oder sollte euer Strom ausfallen). Alle weiteren Vorteile des Mods findet ihr einen Punkt tiefer.

Vorab:
Mein Ender 3 hatte immer Probleme in der Z-Achse, welche auf eine krumme Spindel zurückzuführen waren. Daher habe ich beschlossen den Ender auch in Z auf Riemen umzubauen.

Dieser Umbau löst auch dem Problem einer hängenden x-Achse, auf der rechten Seite. Durch die beiden Riemen, laufen die beiden Seiten nicht nur synchron, sondern lassen sich auch auf den Millimeter genau einstellen.
Sollte man dieses Problem mit der X-Achse haben, ist dies also eine geeignete Lösung.	
Hier findet ihr die Modelle des Hotends und des Nema:
grabcad.com/library/cr10-stock-hot-end-1
grabcad.com/library/nema-17-stepper-motor-22

Voron Parts:
Die Übersetzung der Z Achse ist vom Voron übernommen. Mehr Infos zum Drucker erhaltet ihr hier: 
http://vorondesign.com/
https://github.com/VoronDesign

Die Datein der Übersetzung sind nicht meine Arbeit und daher auch nicht hier hochgeladen. Ich habe lediglich ein Teil angepasst um die Übersetzung an dem Ender anzubringen. Welche Teile ihr benötigt und wo ihr diese erhaltet, findet ihr unter "Printed Parts".

BOM (die Teile vom Ender werden nicht aufgeführt, Schrauben Muttern etc. werden wiederverwendet)
16x M5*8mm 
6x M5*40mm
4x M5*30mm (Für die oebre Strebe,  die originalen werden auch passen, haben dann aber nicht viel Restgewinde)
16x M5 T-Slot Nuts
10x M3*16
10x M3 Nuts
4x 608zz bearing
4x F623ZZ 3*10*4mm Bearing
3x GT2 20 8mm Pulley (bei einem muss der Flansch entfernt werden: https://www.youtube.com/watch?v=RKpxDKYOJYs)
2 Meter GT2 6mm Belt
1x GT2 Belt Loop (6mm wide) - 188mm http://s.click.aliexpress.com/e/ripvAfVQ (Affiliate Link from the Voron Guys)
0.4 Meter Welle (es reicht ein günstiger 8mm Aluminiumstab aus dem Baumarkt, die Welle muss später gekürzt werden) (ihr könnt ZUR NOT auch die Z Spindel verwenden)

Printed Parts
Die Ausrichtung der Teile ist willkürlich. Bitte findet für euch selbst die optimale Ausrichtung heraus.
V2 verwendet die meisten Teile aus V1, ihr findet diese in der V2.zip.

Alle Teile können ohne Support gedruckt werden.
Alle Teile müssen nur einmal gedruckt werden, außer 4x 'Clamp'(für V3 2xTensionerClampV3 und 2x TensionerBlockV3)  und ' 5x 'Spacer2'(2x für Links, 3x für Rechts)
	Wall line count: min. 5
	Infill: 50% oder mehr
	0.2mm Layerhight

Alle Originalteile sind auf der Voron GitHub-Website zu finden (Ich wiederhole, diese sind nicht meine Arbeit!):
https://github.com/VoronDesign/Voron-2/tree/Voron2.2/STLs/VORON2.2/Z_Drive/HD_Z_Drive

Für die Mod finden sich alle Teile hier: https://github.com/kevinakasam/BeltDrivenEnder3.git

Anleitung:
Es werden alle Teile wie auf den Fotos montiert.  Spacer2 sind die hinteren Abstandshalter der V-Slotwheels für die Platte an der die Riemen befestigt werden.
Die Belts benötigen eine Länge von ca. 88cm und werden bündig festgeklemmt.
Die steps/mm  werden für Z auf 400.00 gestellt werden. Sollte euer Ender 3 kein Eprom haben, schreibt 'M92 Z400.00;' in euren Start-Gcode.

Für den Zusammenbau der Übersetzung findet ihr hier eine Anleitung:
https://github.com/VoronDesign/Voron-2/tree/Voron2.2/manuals

Fertig!:) Viel Erfolg und happy printing!

***Englisch Version***

Attention!
I'm not an expert and 3D printing is my hobby. So please be careful when you rebuild your printer and don't just go ahead. For my printer the parts fit perfectly.
Everybody bears the risks of a modification himself.
All parts can be modified as you like. 

Upadte V2:
Compared to version V1 you can reuse all parts of the printer this time. So the conversion is easier, more stable and cheaper. You could even print the pulleys and save money, but I would not recommend it.

The translation is the biggest innovation. It not only increases your resolution in Z, but also the X axis does not drop to 0 as soon as it is out of power (either after printing or if your power fails). All other advantages of the mod you can find one point lower.

First things first:
My Ender 3 always had problems in the Z-axis, which were caused by a bent spindle. Therefore I decided to convert the Ender to belts in Z as well.

This conversion also solves the problem of a hanging x-axis on the right side. Because of the two belts, the two sides not only run synchronously, but can also be adjusted very precisely.

So if you have all these problems with the x-axis, this is a good solution.
	
Here you can find the models of the hotend and nema: 
grabcad.com/library/cr10-stock-hot-end-1
grabcad.com/library/nema-17-stepper-motor-22

Voron Parts:
The transmission of the Z-axis is taken from the Voron. More information about the printer can be found here: 
http://vorondesign.com/
https://github.com/VoronDesign

The files of the translation are not my work and therefore not uploaded here. I have only modified a part to attach the translation to the Ender. Which parts you need and where you can get them, you can find under "Printed Parts".

BOM (the parts of the ender are not listed, nuts and bolts etc. are reused)
16x M5*8mm 
6x M5*40mm
4x M5*30mm (for the top of the frame; the stock will work as well but only have a few millimeter to grip)
16x M5 T-Slot Nuts
10x M3*16
10x M3 Nuts
4x 608zz bearing
4x F623ZZ 3*10*4mm Bearing
3x GT2 20 8mm Pulley (Left,right, Voron pulley. The Motor Pulley is still the 16T 5mm one!!!) (for one puley you have to remove the flange): https://www.youtube.com/watch?v=RKpxDKYOJYs)
2 Meter GT2 6mm Belt
1x GT2 Belt Loop (6mm wide) - 188mm http://s.click.aliexpress.com/e/ripvAfVQ (Affiliate Link from the Voron Guys)
0.4 Meter rod (a cheap 8mm aluminum rod from the hardware store is enough) (you can also use the Z leadscrewbut thats not good for leadscreaw)

Printed Parts
The orientation of the parts is random. Please find out the optimal alignment by yourself.
V2 uses most parts from V1, you can find them in the V2.zip.

All parts can be printed without support.
All parts must be printed only once, except 4x 'Clamp' (for V3 2xTensionerClampV3 and 2x TensionerBlockV3)  and 5x 'Spacer2'(2x for left, 3x for right).
	Wall line count: min. 5
	Infill: 50% or more
	0.2mm layer height

All original parts can be found one the Voron GitHub site (I repeat these parts are not my work!):
https://github.com/VoronDesign/Voron-2/tree/Voron2.2/STLs/VORON2.2/Z_Drive/HD_Z_Drive

All parts for the mod can be found here: https://github.com/kevinakasam/BeltDrivenEnder3.git

Instructions:
All parts are assembled as shown in the photos.  Spacer2 are the rear spacers of the V-Slotwheels for the plate to which the belts are attached.

The Belts need a length of approximately 88cm and are clamped flush.
The steps/mm will be set to 400.00 for Z. If your Ender 3 has no eprom, write 'M92 Z400.00;' in your start code.

For the assembly of the translation you can find instructions here:
https://github.com/VoronDesign/Voron-2/tree/Voron2.2/manuals

Ready!:) Good luck and happy printing!

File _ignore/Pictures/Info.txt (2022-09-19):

Pictures of Prints with the Belt Driven Ender 3

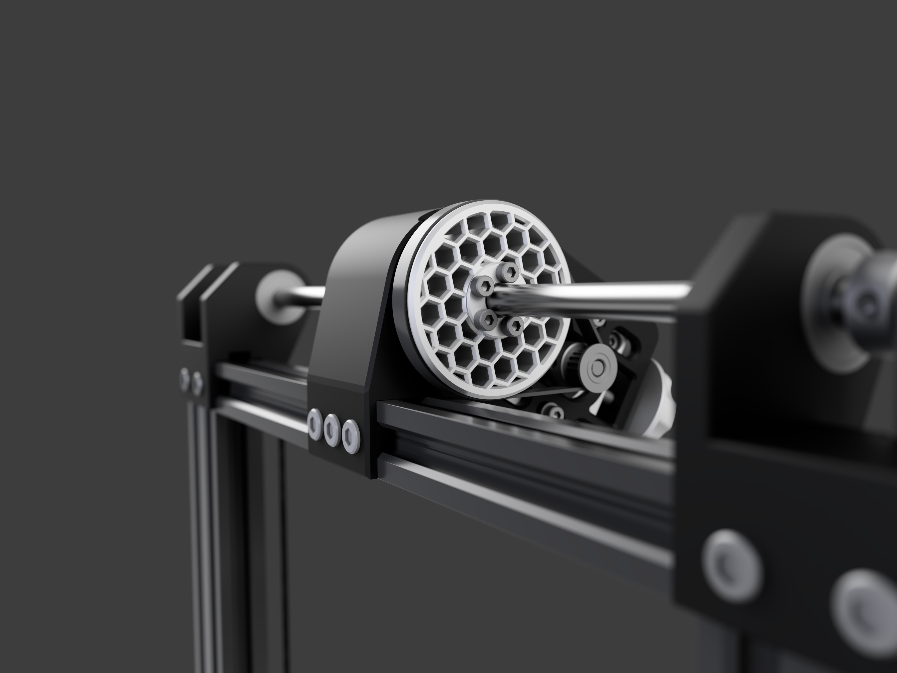
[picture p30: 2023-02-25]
_ignore/Pictures/044bd1ec-a44f-4940-8712-adaad580abfb.png

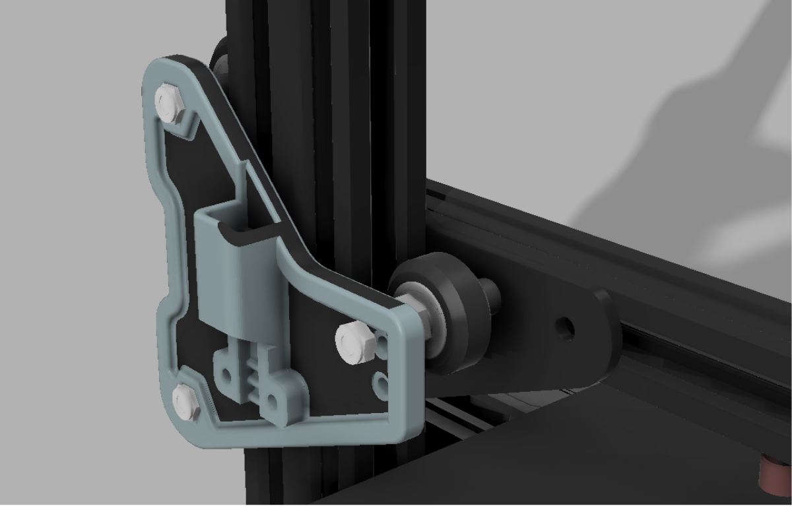
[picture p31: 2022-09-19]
_ignore/Pictures/Right.png

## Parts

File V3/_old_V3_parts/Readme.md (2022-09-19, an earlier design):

All old V3 files in case you want to go back to an older verison.

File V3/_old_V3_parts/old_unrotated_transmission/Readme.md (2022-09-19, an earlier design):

Old unrotated Transmission files before I raised it by 1mm to make it compatible with the rotated version (15.06.2021).

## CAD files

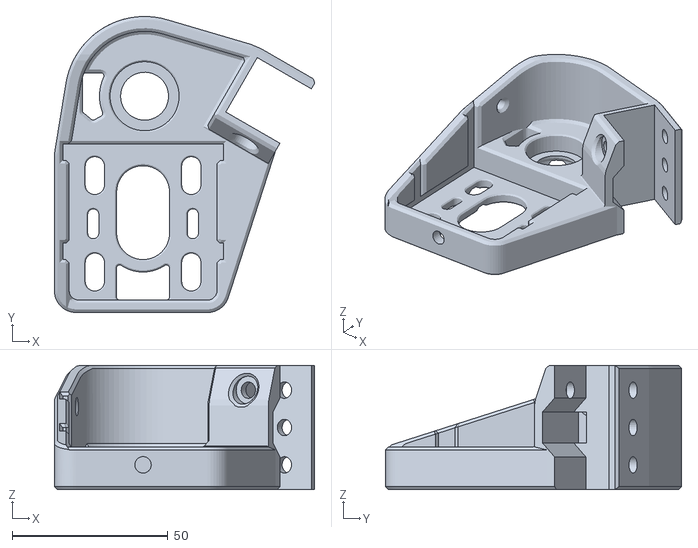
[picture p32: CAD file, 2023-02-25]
_ignore/Configs/DnMB20/1_Transmission_Right_V3.7.stl
83.7 x 95.1 x 40.0

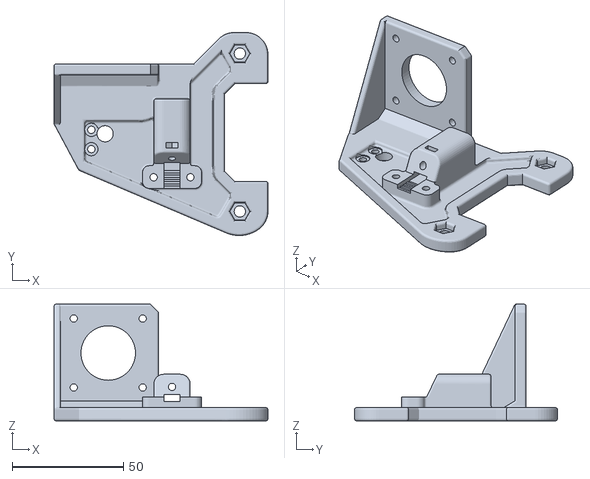
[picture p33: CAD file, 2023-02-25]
_ignore/Configs/DnMB623/1_LeftV3.7_Bowden.stl
96.3 x 91.3 x 52.5

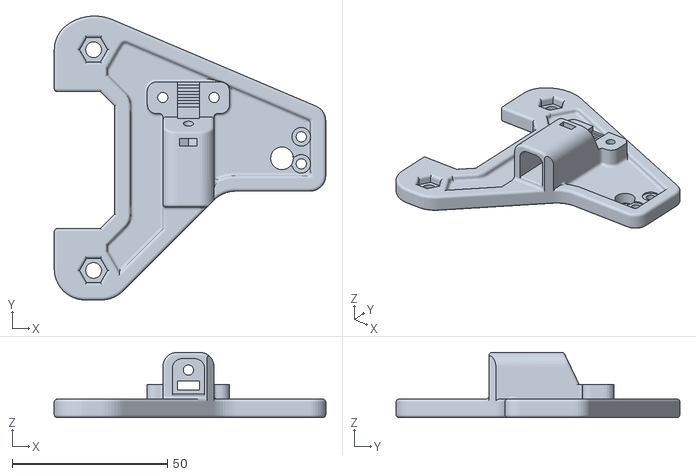
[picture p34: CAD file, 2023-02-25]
_ignore/Configs/DnMD20/1_LeftV3.7.stl
87.4 x 91.3 x 21.0

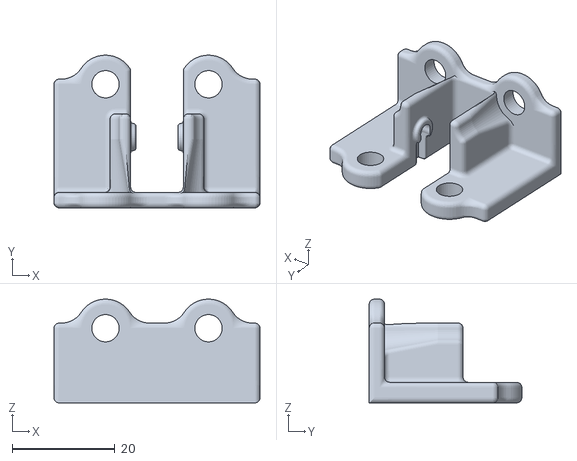
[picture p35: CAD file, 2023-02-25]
_ignore/Configs/DnMD623/2_Bottom_F623_V3.7.stl
40.0 x 29.6 x 20.1

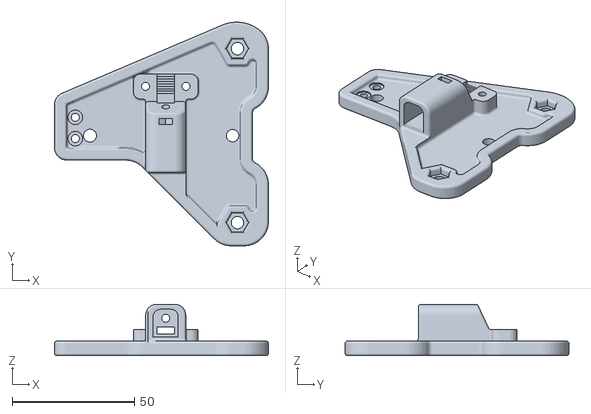
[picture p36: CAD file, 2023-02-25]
_ignore/Configs/DnVB20/1_RightV3.7.stl
87.4 x 91.3 x 21.0

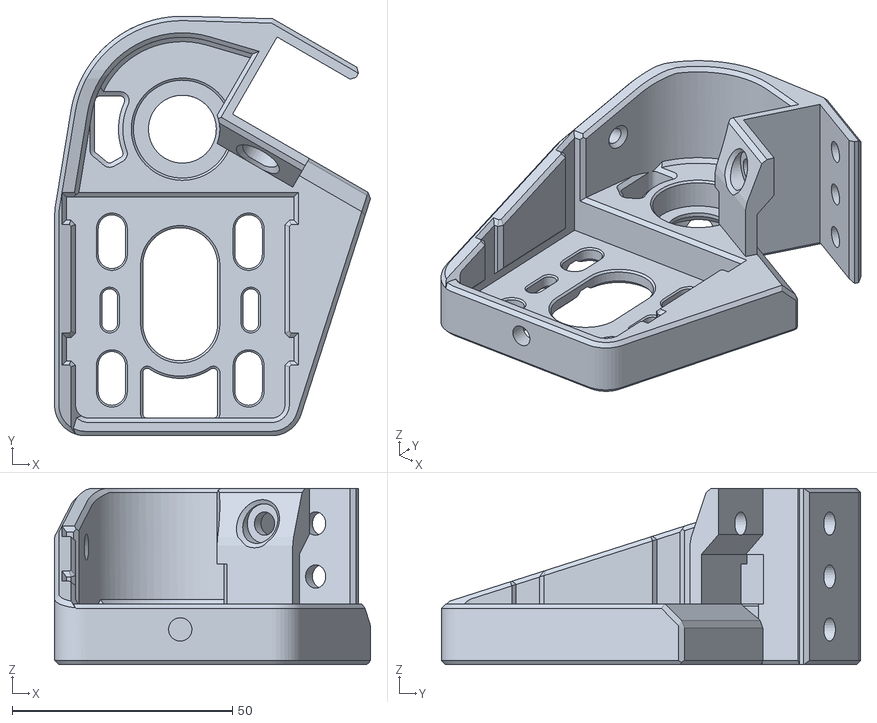
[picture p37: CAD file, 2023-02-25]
_ignore/Configs/DuMB20/1_Transmission_Right_UL_V3.7.stl
71.7 x 95.1 x 40.0

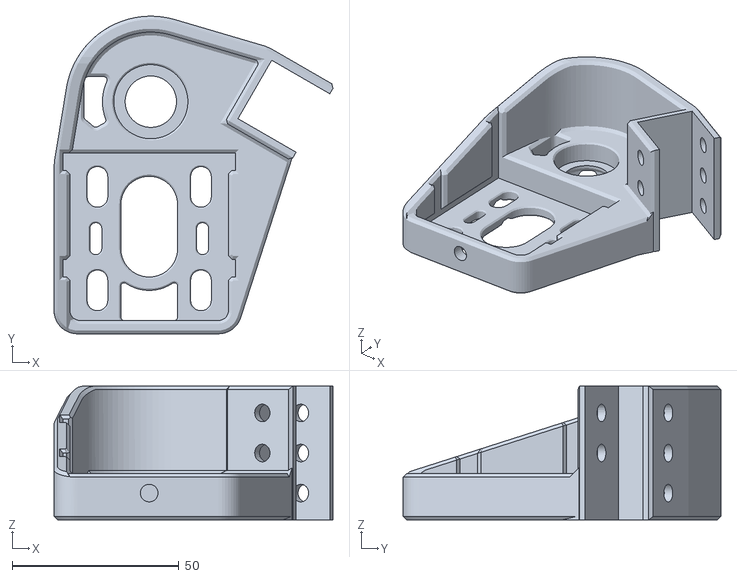
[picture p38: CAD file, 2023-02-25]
_ignore/Configs/SnMB20/1_Transmission_V3.7.stl
83.6 x 95.1 x 40.0

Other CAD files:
_ignore/Configs/DnVD20/1_Transmission_Left_V3.7.stl
_ignore/Configs/DnVD623/1_Transmission_Left_V3.7.stl
_ignore/Configs/DuMD623/1_Transmission_Left_UL_V3.7.stl
_ignore/Configs/DuVD623/1_Transmission_Left_UL_V3.7.stl
V3/1_80TRingGear(Alternative).stl
V3/1_80TRingGear(Voron).stl
V3/1_Power_Supply_Holder.stl
V3/1_RightV3.7_Bowden.stl
V3/2_TensionerBlockV3.stl
V3/2_TensionerClampV3.stl
V3/3_Spacer2.stl
V3/BETA_BottomMounted/BottomTransmission_Leftt.stl
V3/BETA_BottomMounted/CAD/Smooth_Profile_Tops.step
V3/BETA_BottomMounted/Dual Z/2_TopIdlers_20T.stl
V3/BETA_BottomMounted/Dual Z/2_TopIdlers_F623.stl
V3/BETA_BottomMounted/Ender 2/1_Handle_20t.stl
V3/BETA_BottomMounted/Ender 2/1_Handle_f623.stl
V3/BETA_BottomMounted/Ender 2/1_z_endstop.stl
V3/BETA_BottomMounted/Single Z/2_TopA.stl
V3/BETA_BottomMounted/Single Z/2_TopB.stl
V3/BETA_BottomMounted/_Old/DualZ/1_Transmission_A_Left.stl
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

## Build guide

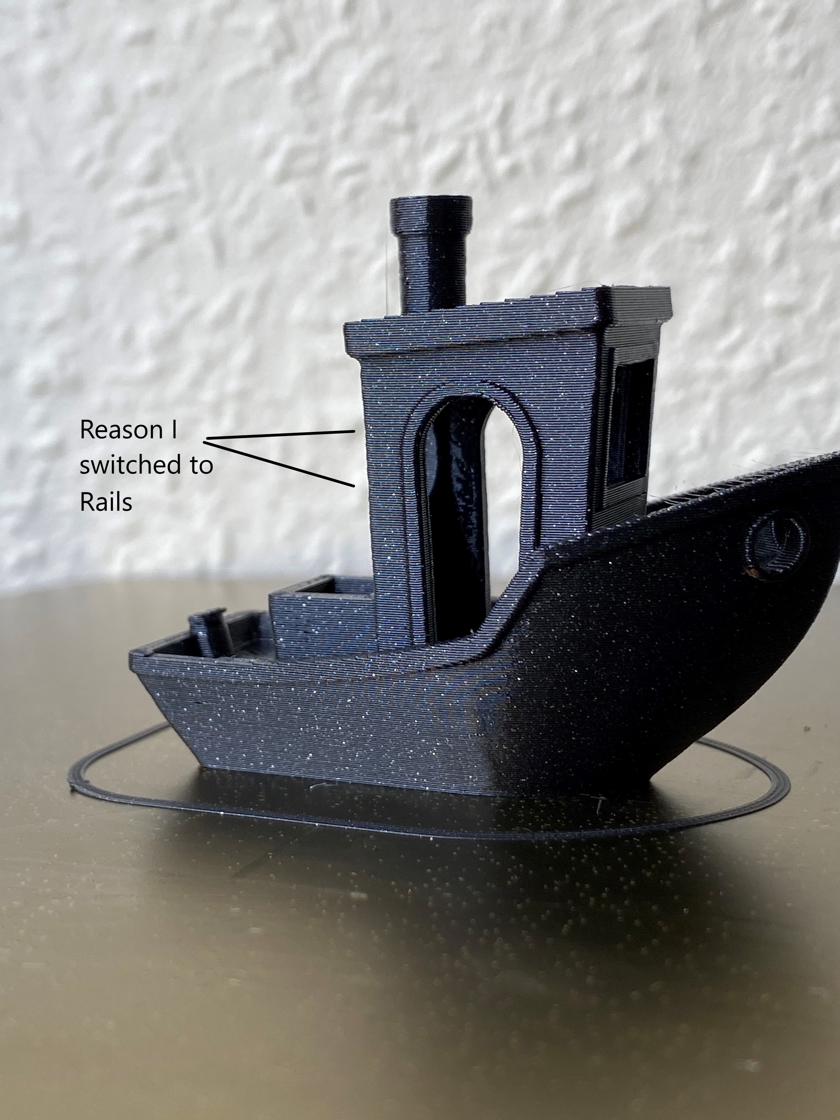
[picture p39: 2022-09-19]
_ignore/Pictures/print_examples/Benchy_error.jpg

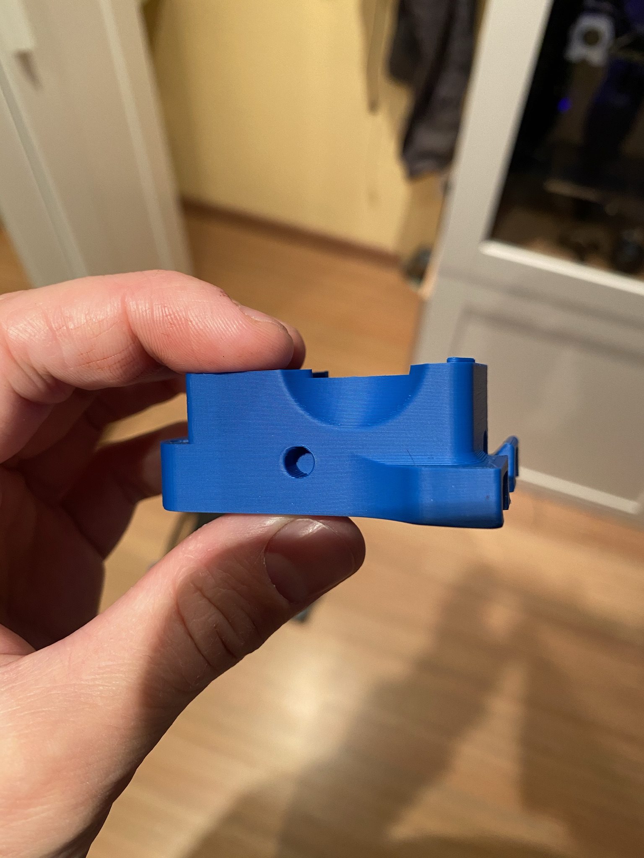
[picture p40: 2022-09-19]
_ignore/Pictures/print_examples/ABS.JPEG

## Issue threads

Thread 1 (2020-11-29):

Can't download

PerLangkjaer, 2020-11-29:
Hello
I can't download the V3.step files.
I would like to check and mabye adjust the Z plates.

kevinakasam, 2020-11-29:
Yes GitHub can’t handle step files. Just download the hole project, you can find the step in the downloaded zip.

PerLangkjaer, 2020-11-30:
Thank you :-D

Closed 2020-11-30.

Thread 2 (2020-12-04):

Z-plates have very thight holes for V-slot wheels

PerLangkjaer, 2020-12-04:
It seems that the holes for the wheels is about 1mm to close to eachother, 0.5mm on both sides of the belt.
At least compared to the CR-10 second Z-stepper plate you can buy of Aliexpress

kevinakasam, 2021-01-04:
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

Thanks for that. Do you have issues with both sides? I updated the Left plate, because some are telling me that this does not fit. I made the gap 0.5mm wider. (And sorry for my late response)

PerLangkjaer, 2021-01-04:
Both sides are tight.
I resized it to 102% and it fitted a bit better.
And its ok with the reply,  X-mas, New Year and Covington...

kevinakasam, 2021-01-04:
okay maybe i should redesign the plates. I modified the Plates from the CAD that Creality supported. So the distance is 60,2mm between the holes. For me everything fits perfect.  I don't understand the problems with the Z-plates. For some they fit, for others they don't

kevinakasam, 2021-01-07:
So I spent some time and fexed the problem with the Plates. I made an mistake eith the drawing of the exentric nut, it was impossible to rotate them correctly, works now:)

kevinakasam, 2021-01-17:
So the files are updated, this issue is solved. Thanks for the hint:)

PerLangkjaer, 2021-01-18:
Hi, sorry for the late answer, ille give it a go when I have some spare time on the printer, but I'm sure it works fine with the updates you made.

Closed 2021-01-17.

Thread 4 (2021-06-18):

Flip motor tensioner arm part for optimal print orientation.

Nopileus, 2021-06-18:
The motor tensioner part is flipped the wrong way for optimal printing orientation, the voron guys have tapered the four motor mount holes so those should face down.
https://github.com/kevinakasam/BeltDrivenEnder3/blob/main/V3/Voronparts/1_MotorMountTensionerArm(Voron).stl

kevinakasam, 2021-06-20:
Hey, thanks for the hint, I will update that;)

kevinakasam, 2021-06-20:
Updated the part

Closed 2021-06-20.

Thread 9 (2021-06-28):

Missing files for transmission

atriptych, 2021-06-28:
Hello,

The .stl files for the entire transmission (both regular and rotated) seem to be missing from both Thingiverse and GitHub. I was able to export the bodies I need from the Fusion360 CAD file, but they seem to be older models and don't reflect the bearing change you made in your changelog.

atriptych, 2021-06-28:
Update. I now see that they are here in the Voronparts folder on GitHub. As this pertains to Thingiverse only, I will close this issue.

Closed 2021-06-28.

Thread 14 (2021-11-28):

LeftV3.3 stl

Viper7016, 2021-11-28:
I just printed the LeftV3.3 stl file and the teeth for the belt are all squished and not uniform. After comparing V3.3 to the previous versions, I see that all the older versions have a proper 2GT belt tooth, but 3.3 has a square 1mm tooth with 1mm spacing.

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

kevinakasam, 2021-11-28:
Hey, thats right. With the V3.3 I have changed the profile. The old profile does not fit the GT2 belt. However, the 1mm squares fit exactly to the belt. The edges are not rounded, so that these can "bite" into the curves of the belt and the belt is very well secured.
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

Viper7016, 2021-11-29:
Thank you for the quick reply!

I apologize for not comparing the belt. I only compared the STL. That v3.3 tooth pattern is the only part of the print that came out poorly. I have no idea why.

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

Closed 2021-12-01.

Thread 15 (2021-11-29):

1_RightBottom.stl too close on gantry

ultrazauberer, 2021-11-29:
Hello,

thank you for the great modification. I could complete it yesterday and made three little observations:

1) the 1_RightBottom part (https://github.com/kevinakasam/BeltDrivenEnder3/blob/main/V3/1_RightBottom.stl) is on my Ender-3 too close to the gantry so the belt starts to rub on the 2040 profile. I fixed it for now by using two washers but 1mm - 1.5mm more clearance would be the best. So a simple increase of the strength ob the baseplate should solve this problem.
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

2) the pulleys on the top let my belt moving left and right an the clearance where the belt should move freely is pretty tight. You can see it in the picture.
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

3) the rod could be 4-5mm longer being in total 335mm. I let cut my rod before I assembled the mod and saw that the rod disappears in the 608ZZ bearings on the right and the left.

But all in all it's a really nice mod and I already did my first testprint and all went fine!

Thanks!

ultrazauberer, 2021-11-29:
I modified today the STL and reprinted the part. Now the part touching the 2040 profile is increased by 1,5mm.
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

I wonder why I am the only one with this issue.

weav2k4, 2022-01-01:
I concur the bottom idler pulley is too close to the vertical.  I will also be modifying the part to increase the clearance to get the belt parallel.  The left bottom and right bottom parts look identical to me so will be changing both. And you are correct as well that the rod needs to be 333mm minimum to be flush with the outer bearing faces.  Cut mine to 335 and have 1mm protruding the bearings.  Excellent mod though and hopefully will get it married to my gantry changes soon.

kevinakasam, 2022-01-10:
Hey, sorry, I forgot about your issue! I uploaded an update yesterday that made some changes to the belt path, I think your problem should be solved with that. Looking at the photos, it seems like you are using pure rubber belts? Are they reinforced (fiberglass for example)? If not, you should get new belts as soon as possible or you will have problems soon. Maybe the belts you are using are a little thicker than the reinforced belts.

ultrazauberer, 2022-01-10:
> Hey, sorry, I forgot about your issue! I uploaded an update yesterday that made some changes to the belt path, I think your problem should be solved with that. Looking at the photos, it seems like you are using pure rubber belts? Are they reinforced (fiberglass for example)? If not, you should get new belts as soon as possible or you will have problems soon. Maybe the belts you are using are a little thicker than the reinforced belts.

I ordered the belts from AliExpress (linked in the BOM). I think it looks fine:
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

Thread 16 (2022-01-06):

G34 Dual Z

aidbish, 2022-01-06:
I cant seem to locate the dual z folder referenced in the read me
is this correct or am i just going blind

Dual Z G34
For a dual Z setup with two z motors use the files from the "Dual Z" folder instead of the transmission and top parts from the V3 folder. The rest is still the same, works with V-Wheels and MGN-Rails.

aidbish, 2022-01-10:
Folder now available

kevinakasam, 2022-01-10:
Oh, sorry, I didn't see your issue!

aidbish, 2022-01-10:
all good mate, thanks for uploading

Closed 2022-01-10.

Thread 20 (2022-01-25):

No step file for linear rail parts

michelluccote, 2022-01-25:
I have been running this belt system over 6 months. I am now upgrading to linear rails but found one of the part does not fit correctly because my rails seem to have a slightly thicker car on them. I tried to modify the STL file for the left adapter but Fusion cannot generate an STL from the original STL. I import  and try to export it back and get an error.

I downloaded the CAD files but this does not include any of the linear rail adapters for the Z axis. Can you please share these files?

kevinakasam, 2022-01-25:
You're right. I'm sorry, should be online now. Are you sure that your rail is to big? the Left parts slides a bit onto the rail like you can see on the photo. Maybe this helps :)
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

michelluccote, 2022-01-25:
Thanks for the fast reply. I'll take a look.

I bought some Twotrees MGN12N linear rails and they do seem thicker. Here is the link to them on Amazon.

https://www.amazon.com/gp/product/B07SN6MT6T/ref=ppx_yo_dt_b_asin_title_o08_s00?ie=UTF8&th=1

And a few pictures of the carriage aligned with my printed bracket. Everything else appears to align except for that thickness.

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

michelluccote, 2022-01-25:
I have downloaded the new STEP file and it has everything I needed. Great work by the way. I love this upgrade.

Closed 2022-01-25.

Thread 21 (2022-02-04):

CAD - MGN 12H Rail

HermanGaviriaMarin, 2022-02-04:
Lord Kevinakasam,

Your designs are flawless, they print perfectly fine, they work great. I can't express how glad I am to have found your mod for the ender series printers.

I'm working on modifying my printer to accommodate for several extruders, moreover, I'm working with your MGN v3 design to use dual linear rails on the Z axis. Currently your cad model uses the v-slot wheels and there are no signs of the spacers you created for the linear rail variant of the mod, if it isn't too much to ask, would it be possible for you to post the CAD models to the other variants, more specifically one that has the spacers that replace the v-slot wheels?

Just to give you a little sneak peak here is a view of what I'm working on, to give you a little hint it involves the Octopus Board, 5 extruders, and a custom ultra silent fan shroud which uses noctua fans. Btw the motors up top are extruders and not the x steppers. Of course I was unable to change the model to reflect on your mod, not just yet, I was kinda hoping to get the spacers first (the step file from you) then I'd go in there and change things up
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
This is pretty messy at the moment because I have not been able to take care of the wires but as soon as I have the extruders mounted where I need them then I'll do cable management.
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

Thank you for your all your hard work, your mod really helped me.

kevinakasam, 2022-02-04:
Hey :D
Thats a huge project, 5 extruders will give you many colors thats cool! And I really like your Switchwire themed electronics box.
 So you mean the MGN Spacers arent included in the step file? Have you checked the last update of it? I thought I included everything, if not I'm very sorry and I will upload a full step file asap!
 One question though, are both z motors connected to the same rod?

HermanGaviriaMarin, 2022-02-05:
Grandmaster Kevinakasam,

Yea its a big project, I've been working on it for a while now. I will share all the step files with everyone once I'm done building it though to the truth is that this mod isn't really for everyone, only for those who have an octopus and plan on using it with a Bowden styled ender 3 series printer. However, the legs that I made I can most definitely say that many will come to like them as they are very strong and will be modular, as on now they only accept squash balls but I will make versions that use the old rubber feet as well as other feet that can be rigid mounted into wood with screws. Most of the things you see in my design are support free like your designs.
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

I'm sure you didn't include the part because in the CAD you provide the mod is using the V-slot wheels which is totally understanble, if there weren't any linear rails than that specific piece didn't need to come up. I just happen to need it so that I can design some mods to accommodate for an extruder that happens to be located next to the secondary extruder mount you created. I could design my own spacer but I sorta want to keep your design as original as possible. It would be a huge help to have the cad with the all linear rail (dual linear rail) version on the mod.
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

To answer your question about how I have those two motors connected to the same shaft while also being wired in parallel, the answer is very simple, I changed the polarity of one of the coils in the mirrored motor/transmission. Basically all I did was switch the A+ and A- to make the motor turn in the opposite direction, at the same time I left the other motor alone to spin in the normal direction. The result being that the motors will turn in the same direction despite being mirrored. I first performed this using the creality steppers which are wired with this sequence of coil sets: A+ X  B+ A- X  B-   <-- imagine that as the JST connector found on the stepper motor the x is just the pin in between that isn't used.  I'm sure you know all about this but I put all this info here just in case someone looks at this and has the same question
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

I have got some questions about your ender 3 afterburner design. More specifically the cable chains or drag chains. The drag chain that you have located in the Z axis (not the one on the X axis), where does that drag chain mount to in the bottom? I understand that it is  connected to the limit switch box that you designed but what about the bottom portion of that drag chains? I also want to add drag chains to my design but I will need two sets of Z drag chains because I will have those two extruders on the left side of the X axis.
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

weav2k4, 2022-02-05:
I believe Kevin may be confused as I am about why you need two z steppers if they are joined?  You can just use a single stepper if not trying to do G34 with separate Z's.  Is it just so you have stronger Z action?  Very interesting and ambitious things going on here.  Curious to see how it all turns out for you!

HermanGaviriaMarin, 2022-02-05:
Weav2k4 I totally understand where you're coming from, my design is definitely not conventional in several ways but I'll try to point out my criteria and why I'm doing things like this.

First, just as you briefly mentioned, yes it does have to do with the strength of the Z axis, the motors I'm using aren't per say extremely heavy, but there will be 4 of them in the X axis, that weight adds up, and though I strongly believe that one motor is likely to be enough I also like to play it save, thus having two motors.

As to why I'm not running them individually. Well I really liked the idea of having independent motors, but I came to small conclusion that I have yet to have answered, I will create some illustrations for you so you can see where I'm coming from, please bare with me and my microsoft paint sketches.

G34 was made to correct a skewed or non horizontal X axis on printers that have individual Z motors. The procedure is performed with a series of measurements taken from a bed probe such as a CR-Touch or BL-Touch, this probe measure the difference in height from across the bed in the horizontal distance of the X axis, it corrects this by adjusting the motors on each side of the Z axis individually to either raise or lower the gantry right? This is displayed below.
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

But now lets explore what would happen if the bed is not in an ideal position. Assuming that the bed of the printer is perfectly leveled (and i don't mean tramming, I mean true leveling) then the X gantry will undoubtedly become perfectly horizontal and no side of the X gantry will be higher than the other (i.e the left side of the gantry is 2 mm higher than the right side of the gantry). But what if we perform a G34 and the bed is all sorts of ways skewed out of position? the G34 will perform what its being told to do, and that is make sure that the the left and right side of the X gantry are at the same height with relation to the bed thus the illustration below.
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

Thus we are left in the same place where we started, the X axis is at an angle instead of being perfectly horizontal, yes it is not parallel to the bed but in the long term this will deform one or more components of the X gantry.
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
dwery, 2022-02-10:
I do like screws. No hurry, don't wait for perfection, but don't settle for anything less than very good either.

kevinakasam, 2022-02-10:
Good morning @HermanGaviriaMarin
First of all, thank you for your detailed answers and the time you invest in your explanations. Therefore, I would like to answer you back a little more detailed. I'm currently in the middle of the exam phase and just have very little time and in the evening I'm usually tired and go to sleep early, which is why my answer took so long. So I want to give you some constructive feedback, please don't take this as simple criticism, they are just ideas :)

So your explanation about the G34 is correct, it aligns the axis to the bed and if that is crooked, the axis is crooked too. This is why you need a joint and a length compensation in your axis, otherwise you manage the leveling only by bending the plastic. That's why the Dual Z solution is not ideal at the moment. Regarding your project: Why did you mount both Z motors on the same rod? This makes a G34 and Tram Z physically impossible. No matter which of the two motors turns, it will always have the same effect. And since you have the two motors running in parallel, they can't rotate differently. That's the way I have it too, but I don't have them both connected to one rod, so the right and left side are controlled by the same motor signal, but by a Tram Z the axis can still align itself (e.g. the left side stops at its physical endpoint and skips steps until the right side also comes against its physical endpoint). This way the right and left side can be adjusted independently, with Tram Z but not with G34. For G34, the motors must also not be wired together, but each needs its own driver. With your setup you only have the same functions as with a single Z because they are both on the same rod. This might also be quite harmful for the electronics. The two motors may work against each other if they don't run exactly the same. That might demand a lot of current which might destroy your drivers in the long run.

I'm glad you found all parts in CAD, but I didn't change them, as you can see on the timestap. But I also sometimes get confused with all the CAD versions I have ;D

And I really like your mod with the grids at the bottom, it's just so it's not too high but it should give enough space to put the electronics inside. But I'm not so convinced about the feet. These squashballs make the printer much quieter but also much more unstable. at higher speeds the printer wobbles like a boat on the sea. Look at the squash feet of the Prusa bear (https://www.prusaprinters.org/prints/20292-low-profile-v-slot-squash-ball-feet-prusa-bear-log) they are just about ok, because the center of gravity of the printer is much lower compared to when the printer is above the squash balls. This makes it more stable, maybe that would be worth a thought? I once had a mixed solution on my printer, for this you cut the balls in half. The ball was filled by the foot and only the thick rubber damped the vibrations, but not the air in the ball. This makes the whole thing much more stable (similar to this, but the ball was filled in the middle by the print https://www.thingiverse.com/thing:3895933).

I can understand why you took the big fans for your part cooling, they are nice and quiet. But these "normal" fans are not really suitable for part cooling, because they don't have enough pressure and volume flow. The radial fans have the advantage that they are very strong, which is very good for part cooling, because we want to cool quickly and strongly if necessary. Only in this way the plastic can harden faster and the warm air can flow away. For materials that need little air, this may work, but I'm not sure if they can really keep up with one or two 5015.

My drag chain goes directly to the electronic case at the front. I just connected the chain the other way around in the midde to get the S shape. Like you can see here:
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

I am excited about your results with the 5 colors, I also had a MMu2, but never used it and then sold it again. Now I have an Idex and I can use at least two colors. And do you want to mount all three or five motors on the X axis? Don't you think that will be a bit too heavy? Also, all the motors on top of the printer make it very top heavy which should give you a lot of vibrations. I would try to mount them on the side of your printer with two additional aluminum profiles. Like this maybe:
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

So I think I have said something to all points. I am really curious to see how your printer looks like in the end. And I will definitely have a look at your electronics case design. I like that!

kevinakasam, 2022-02-27:
@HermanGaviriaMarin any Updates?

Closed 2022-05-10.

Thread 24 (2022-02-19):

1_ZDriveTensioningRing(Voron).stl too large

kitcarfreak, 2022-02-19:
Printed everything in ASA on my voron v0.1 which is calibrated very good and had to print 1_ZDriveTensioningRing(Voron).stl with 98% size in X&Y to have a good fit with the thread of 1_MotorMountTensionerArm(Voron).stl

at 100% it just slides over

kevinakasam, 2022-02-21:
Hello, I did not design these parts, I took them from Voron. They already calculated the shrinkage of the parts, maybe you have activated the shrinkage compensation?

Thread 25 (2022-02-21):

UltraLowHeight says same BOM, but it looks like the 188mm belt should be shorter.

cdschris00, 2022-02-21:
Looks like the 8mm rod gets moved down for ultralowheight. Is there a different belt length mentioned somewhere?

kevinakasam, 2022-02-21:
Hello, no the looped belt is just the same as for the normal versions.

Closed 2022-05-10.

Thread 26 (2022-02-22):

braces support addition

xjustbmw, 2022-02-22:
Are there any plans to add frame braces support on this version ?:)

Similar to this https://www.thingiverse.com/thing:3746653
I think this is the perfect Z axys combination for ender printers
My stock ender 3 printer had ~4mm deviation on top without the frame braces installed

Alfiegerner, 2022-02-23:
Was just about to ask something similar.

I'm upgrading to dual z from single motor.  Previously the two holes on for top left and top right on the standard belted version were just the tight size to fit the standard AliExpress bracing kits, but the dual z 3 bolt set up won't allow it.

xjustbmw, 2022-02-23:
We can surely mix the two parts together. But I think a new verion here for evrery one to enjoy would be nicer and have the printer way more rigid and square at the same time :)

kevinakasam, 2022-02-23:
Hello to both of you. Tbh I'm not the biggest fan of these support rods, but if you'd like we could add something similar to the mod. Should be pretty easy, especially with the normal top parts. And there should be a way to add it to the Dual Z setup as well

Alfiegerner, 2022-02-23:
Thanks @kevinakasam . Out of interest how come you don't like these braces? Just wondering if I've missed something.

Also, my print quality is so much better since doing this mod, really chuffed 🙏

xjustbmw, 2022-02-23:
Thanks again kevin for considering.

For me the quality really improved as well, but I also did dual Z rods, and direct drive with bmg/e3d all metal hotend at the same time.
Took me a few hours to align them properly so it runs smoothly. but i would still like to move to belts in the future.

I think this braces only help if the gantry is not perfectly perpendicular from the factory, and if you print fast and tall objects. But surely they cannot hurt the printer . its way more rigid than before.

xjustbmw, 2022-02-23:
speaking of the future, any recommended better V slot wheels ?

kevinakasam, 2022-02-27:
could one of you cantact me via discord please? So we can talk about the additional support:)

xjustbmw, 2022-02-27:
sure. i just sent you a friend request. thanks

kevinakasam, 2022-05-10:
I've added a folder in V3_extras. I will close this now :)

xjustbmw, 2022-05-10:
thanks a lot for this, i am planning to print this soon
my printer works fine at the moment using the dual Z screws, but at the first error i will change it to belts :) already got all the required kit parts :)

Closed 2022-05-10.

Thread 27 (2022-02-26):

Ultra Low Transmissions do not have through holes

kiloalpha628, 2022-02-26:
I printed the STLs for the Ultra Low transmissions (left and right) and to my surprise, the holes for the T-nuts/bolts do not extend all the way through the model. I finished with a drill so it was not a issue but others may not have this ability. Thanks!

kevinakasam, 2022-02-27:
Ah thanks for the reminder, I updated the files!

Closed 2022-05-10.

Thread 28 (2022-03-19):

Unequal belt path length for left and right belts in version 3.5

maxkueng, 2022-03-19:
Hi. I tried to upgrade to the V3.5 plates but I ran into an issue.

The distance from the top of the nut to the bottom of the belt clamp (see image below) is different for the left and right plate. The left distance is 19.405mm and on the right it's 20.629mm (blue dotted line in the image below).

This means that the required belt lengths are not the same for the left and right belts and therefore it's not possible to achieve equal belt tension on both sides without measuring the actual tension.

I took the same measurements from an older CAD (I don't know which version or how old) and there both distances are equal.

The method I use is to cut both belts to the same length and then tighten the tensioner screws with an equal number of turns. But for that the belt paths on both sides must be exactly the same.

The measurements below were taken from BeltDriven_Ender3_V3_25012022.step and I've also been able to measure the difference in the actual prints.

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

maxkueng, 2022-03-19:
Here's a Gif of how I fixed the RightV3.3 plate so that the belt paths are equal. I shortened the belt path on the right plate so that it's the same as for the left plate.

I don't have Fusion 360 so I did it in Onshape. Here's the link:
https://cad.onshape.com/documents/530c50c0feb35506422f7b54/w/d6230fb67fb3cda85e9c2f90/e/6c6611e621e6919f323474aa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

kevinakasam, 2022-03-20:
Hello!
also thank you very much for this hint! I am wondering how this error could happen since I mirrored the plates, but I will fix this as soon as possible. I can't believe you caught this problem^^

aidbish, 2022-05-06:
@kevinakasam was the files updates or is it best to use @maxkueng version above to resolve this.

maxkueng, 2022-05-08:
@aidbish In case you need it, here's a Zip with STL and STEP versions of the fixed part. I couldn't upload the STL directly because GitHub doesn't support it.

[BeltDrivenEnder3 - RightV3.3-fixed.zip](https://github.com/kevinakasam/BeltDrivenEnder3/files/8647390/BeltDrivenEnder3.-.RightV3.3-fixed.zip)

aidbish, 2022-05-11:
@maxkueng Thanks mate, appreciate it

maxkueng, 2022-12-03:
@kevinakasam It looks like this has been fixed in V3.6. Can you confirm?
While I haven't printed the new version, I did check the new 3.6 CAD and it looks like the belt paths are now the same length.

So maybe you can close this issue.

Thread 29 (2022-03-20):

Easier to insert nuts of MGN12H adapter from the bottom

maxkueng, 2022-03-20:
Hi Kevin / Sam

I had some trouble inserting the M3 nuts into the block and pushing them all the way down, probably due to ASA shrinkage. So I've moved the holes to the bottom where the nuts don't have to be pushed down through the entire part. I thought you might want to consider doing the same for your original design as it makes it much easier to insert the nuts.
On the left side it's not really an issue because the nuts don't have to be pushed in as deeply as on the right side.

I've attached STL and STEP files here for reference: [RightV3.3 (MGN) bottom nuts.zip](https://github.com/kevinakasam/BeltDrivenEnder3/files/8310476/RightV3.3.MGN.bottom.nuts.zip) (sorry GitHub does not support directly attaching STEP files and STLs)

I don't have Fusion 360 so I just patched up the STEP file with lots of booleans but here's the Onshape link:
https://cad.onshape.com/documents/530c50c0feb35506422f7b54/w/d6230fb67fb3cda85e9c2f90/e/e698622b87cb5f67726b5bd5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

kevinakasam, 2022-03-20:
Hello!
Very interesting solution. I'll take a look at it, too bad I didn't come up with the idea sooner. Thanks for sharing!

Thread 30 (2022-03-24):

Left/Right Top AB for Rotated transmission

ljruiten, 2022-03-24:
So please correct me if I'm wrong, but I'm trying to find in the documentation how I could have known that the parts I printed were not compatible.
From this Git I took the latest version, and printed the transmission body with bearing and rotated version. Then according to BOM I printed the left/right top A/B, but they don't align with the rotated transmission body for the rod. Looking at the STL files they do align with the unrotated version though. The only bearing holders that seem to align with the rotated transmission body are the TransmissionBody_Left.stl and TransmissionBody_Right.stl in the root directory. This seems like there's a line missing in docs/BOM maybe?

ljruiten, 2022-03-24:
See this picture this is:
- BeltDrivenEnder3\V3\Voronparts\1_transmission_rotated_bearing.stl
- BeltDrivenEnder3\V3\Voronparts\1_RightTop_A.stl

Perhaps what I didnt get is that the rotated version IS the ultra low version, but if you look at attached picture the two holes for the bearing don't line up if you put them on top of the frame.

The what you call "ultra low version" does seem to be compatible with the rotated version. Just wasn't clear to me that those two belonged together.

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

kevinakasam, 2022-03-24:
Or this top part for your transmission: https://github.com/kevinakasam/BeltDrivenEnder3/blob/main/V3_Extras/UltraLowHeight(Ikea_Lack_Enclosure)/Single_Z/LeftTopA.stl

kevinakasam, 2022-03-24:
So this are the normal files (not the ultra low version)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

ljruiten, 2022-03-24:
Ok, well I think I rather reprint the tranmission than the top parts. Just thought the rotated version looked a little cooler. I get it now.

Have to say: it is a little confusing to find the right set of files.

ljruiten, 2022-03-24:
Anyway I'll close this issue. Thanks for the support

kevinakasam, 2022-03-24:
You just have to print the files from the V3 folder and pick a transmission body you want (rotated or unrotated/withbearing or without) I'm sorry for the stls in the root folder, I guess that was the issue

Closed 2022-03-24.

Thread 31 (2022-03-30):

V3 2_Bottom_toothed20T.stl seems to be the same file as 2_Bottom_FG23.stl

Amor-Roma, 2022-03-30:
[2_Bottom_toothed20T.stl](https://github.com/kevinakasam/BeltDrivenEnder3/blob/main/V3/2_Bottom_toothed20T.stl)
[2_Bottom_F623.stl](https://github.com/kevinakasam/BeltDrivenEnder3/blob/main/V3/2_Bottom_F623.stl)

I bought the recommended motion kit on Aliexpress.  I got the one with 20T idlers, but the printed part seems too small for them.  Is the correct file posted?  It seems like the F623 and the 20T file are identical.

Amor-Roma, 2022-03-30:
I didn't remove the flange. My fault for not reading

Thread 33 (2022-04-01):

Ender 3 V2 Cannot Use Tram Macro

reffu42, 2022-04-01:
The stepper drivers on the Ender 3 V2 are in standalone mode, and their current cannot be adjusted via klipper/firmware. It might be wise to just put a quick note in the Dual Z readme page that the given macro won't work for people with a stock Ender 3 V2 board (Creality 4.2.2 or 4.2.7 boards)

kevinakasam, 2022-05-10:
I did that thanks!

Closed 2022-05-10.

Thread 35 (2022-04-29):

Thin Walls

Biz810, 2022-04-29:
Is it possible to improve top right and left? The place where the belt is tightened always tears me. If the walls were thicker, the problem would be solved.

kevinakasam, 2022-04-29:
Hi, I'm not sure what you mean, the belt gets tensioned on the z plates. How is this affected by the Top Parts?

Biz810, 2022-04-29:
Sorry my mistake I mean the files Left Right V3.5.
I have to tighten the belt really hard. And that tears my filament
there where I go in with the tensioner block.

Biz810, 2022-04-30:
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

maxkueng, 2022-05-08:
@Biz810 What material did you use?

If tightening the tensioner block causes your part to split you might have a bit too much plastic on the Left/Right V3.5 plates from bridging and then the tensioning block acts like a splitting wedge when screwing it in. You could try filing the plate with a small file so that the tensioner block slides in smoothly. Try to get rid of any "hanging" filament from brdidging. The tensioner should move freely so that it will release the tension when loosening the screw

You can also try to shorten the belts by a few teeth (test in 2 teeth increments) so that you don't have to screw in the tensioner block so deep that it splits the plate.

Biz810, 2022-05-08:
It was printed from PETG.
I have reprinted the parts and will try to implement your tips.

Thank you very much

maxkueng, 2022-05-08:
Cool! Just to be clear, I highlighted in red the section of the part where you might want to sand off any lower-hanging plastic from the overhangs.

If the tensioning block requires force to slide into that tunnel because the tolerances are too tight, even after you've sanded off the overhang, sand the edges of the tensioning block instead. That should be much easier than filing the tunnel of the plate from the inside.

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

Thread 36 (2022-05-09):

Request - Geeetech A20(M/T)

rbarreiros, 2022-05-09:
Hello,

After I did this to my creality printers, I realized this is too good to not have in my other printers, which are geeetech a20 (M)
I found an STL with a complete A20M in thingiverse, but, scale seems off, I'll try to figure it out tomorrow, but, I don't have enough knowledge to fix the Z plates to match the A20 plates, as far as I know, it's the only thing that needs fixing, apart from probably have to drill 4 holes to screw the Z belt idlers in the bottom of the printer.

Is it something of a possibility this, or any chance of a fusion file with history so I can try and replicate the work for the A20 Z plate dimensions ?

Thank you for this excellent work

kevinakasam, 2022-05-10:
Hi, thanks for your suggestion! Could you join my discord to talk about this(link in description)? Maybe we can get you the files you need :)

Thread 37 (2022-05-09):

LeftTop and RightTop missing top holes

esteejus, 2022-05-09:
LeftTop and RightTop parts both AB and not seem to be missing the top holes for the frame.

kevinakasam, 2022-05-10:
Hello, the latest version no longer has these screws. You no longer have to unscrew the top beam :)

stuomas, 2022-08-14:
I recently needed to do some x-gantry reworking that involves removing the top bar so I can remove the gantry. Without the holes in the top, it becomes very hard to remove the top beam. At least I would prefer to have the holes, just for easy access.

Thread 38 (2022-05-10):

Klipper Rotation Distance OR ESteps

MahmoudHassib, 2022-05-10:
Hello, Perfect Mod
But what is the Prober Rotation Distance after upgrading to this mod since we are changing from normal T8 Leadscrew

igor-arkhipov, 2022-07-21:
Same as before, rotation_distance = 8

Gear and pulley comes from Voron 2,  here is example config – https://github.com/Klipper3d/klipper/blob/master/config/kit-voron2-250mm.cfg#L86

kevinakasam, 2022-07-26:
Hey,
I now it's been some time but I haven't checked the issues tab for a while, sorry. The mod works with the stock settings, but for Klipper you could add the gear ratio, like this:

`rotation_distance: 40
gear_ratio: 80:16    
microsteps: 16
full_steps_per_rotation: 200    #200 for 1.8 degree, 400 for 0.9 degree`

MahmoudHassib, 2022-07-26:
@igor-arkhipov @kevinakasam
thanks ,i can assure it works as same as in marlin with out any change if you are using normal T8 lead screw , but mainly i was concerned in regards to Klipper and the gear ratio  value with the rotation distance .
@kevinakasam  it would be nice if you can add  Klipper Rotation Distance and Estep's in the manual

MahmoudHassib, 2022-07-26:
@igor-arkhipov @kevinakasam
thanks ,i can assure it works as same as in marlin with out any change if you are using normal T8 lead screw , but mainly i was concerned in regards to Klipper and the gear ratio  value with the rotation distance .
@kevinakasam  it would be nice if you can add  Klipper Rotation Distance OR Estep's

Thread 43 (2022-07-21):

Max Velocity and Acceleration on the Z axis after installing this mod?

nikoraasu, 2022-07-21:
I was wondering if I can change the default velocity of 5 and acceleration of 100 to something faster now that I have this mod?

PhenixNoir, 2022-07-25:
I'm using 50mm/s for z velocity and 500 acceleration. Works great for now!

kevinakasam, 2022-07-26:
You shouldnt need higher speeds than stock, at least for printing. I'm using quite fast travels for homing and probing, up to 100mm/sec. Acceleration is set to 300 :)

Closed 2023-10-13.

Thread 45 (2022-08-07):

Transmission_UL

phanthuat, 2022-08-07:
I'm on version 3.5 and am planning to switch back to v3.6 UltraLow.
Can you update the file Transmission_UL_V3.6 for the left side? because if using the right file, the stepper motor cable will have to be much longer? thank you very much

kevinakasam, 2022-08-07:
> I'm on version 3.5 and am planning to switch back to v3.6 UltraLow.
>
> Can you update the file Transmission_UL_V3.6 for the left side? because if using the right file, the stepper motor cable will have to be much longer? thank you very much

Hey,
You can use the left side file from the dual z version. It's just mirrored. This way you can also mirror the top parts for the other side (just do it in slicer). If that's too complicated join my discord please and give me a ping there, this way it's easier for me to keep up with all the requests :)

phanthuat, 2022-08-07:
oh, it's so simple I couldn't think of it, thank you so much

Closed 2022-08-07.

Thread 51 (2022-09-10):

Feedback - New belt tensioner nut design

Praelia7or, 2022-09-10:
I had some issues with the new belt tensioner bolt design - the change from inserting it on the bottom to sliding it into a gap (I used V3.6). My nuts didn't fit, either they are slightly larger than standard or my print came out a little small - this is likely as my calibration tests did show inner diameters to be about 1-2% undersized, but they're incredibly difficult to get into to modify after printing, and after you resort to trying to push them in with heat and ruin one, a pain to try and reprint when your printer is in parts! The previous design was a bit fiddly to get the nut set in position but more reliable imo

These either need a lot more clearance to allow you to easily insert of a range of different nut sources or a rethink on the design, I realise with the current design it does need to be tight enough to hold the nut as you tension the belt too.

I know not everyone will have them available and may be too much hassle to maintain a design fork but a version of the parts with heatserts would be fantastic - they are great for 3D printed parts.

kevinakasam, 2022-10-28:
Hey, thanks for the feedback! I made a heat insert version some weeks ago, I waited  with the release so we could test if everything last long enough. Hr_Raven from my Discord tested these for 3 weeks now. Guess they're good to go. I will add them to the V3_extra folder :) Thanks for the reminder!

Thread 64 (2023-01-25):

Ender3 v2 neo uses different extrusions

kandrejevs, 2023-01-25:
An issue I have encountered is that the new "neo" update to ender series uses different extrusions with 1 side flat.
It is still fine in my opinion since support is held with 2 screws and motor mount with 3 if you rotate extrusion 180 degrees.
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

shuff57, 2023-02-09:
@kandrejevs I modified the files to work on an elegoo neptune 2 which appears to have the same style of extrusions. If you're interested, I can send/attach the .stl files of the modded parts along with some pictures?

jonathanysp, 2024-02-28:
@shuff57 This is an old issue, but i'm interested in your modified stl files that would work with new style of extrusions.

Sartium, 2024-03-01:
@jonathanysp I just upgraded my V2 Neo to the Z belt and I found it easier to just buy a new 2020 extrusion and cut/drill it. Took 10 minutes if you have the tools.

shuff57, 2024-03-02:
@jonathanysp I can't attach .stl or .3mf files so I'm adding google drive link for you get the files. I'll try to add some pictures in there too.

[Elegoo Neptune 2 - Belted Z Mods](https://drive.google.com/drive/folders/1ToEX0puyeLmGaZNeT88EKgmVN3ZtdQ0N?usp=sharing)

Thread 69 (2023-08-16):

188mm belt to 188T belt

sepkov, 2023-08-16:
Hey there, thanks for this awesome mod.

I did run through parts list to make mine, I stumbled on a part which I couldn't find. On the parts list it says 188mm belt and on the bottom it says 188T. I couldn't find the source code of the website to create MR.

Thanks and have a nice day.

Parts list I'm looking: https://kevinakasam.com/snvb623-2/

kevinakasam, 2023-08-17:
Thanks! I'm going to fix that, 188T is correct, 188mm is wrong.

Closed 2023-11-16.

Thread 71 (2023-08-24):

Linear rod with belt driven z

ercintorun, 2023-08-24:
Kevin, would you consider doing a new design for belt driven ender using linear rods for X and z Like this one:
https://www.reddit.com/r/3Dprinting/comments/p7ewyc/i_was_really_tired_of_ender_wheels_getting/

DrBoofenshmirtz, 2023-09-02:
I just left that exact suggestion on the discord... I second the motion... I'm going to attempt to modify it myself in the mean time...

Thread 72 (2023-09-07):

Motor Mount Tensioner Arm

Billy-d-Kidd, 2023-09-07:
Excellent work on this project. I did notice a thing or two while building it.
For the heat set insert version, would it be possible to add a short M5 insert where the M5 tensioner ring bolt goes into the motor mount? This way when loosening the belt you don't go to far and that M5 nut fall out. Might also be able to add a spring between the mount and the transmission body or the transmission body and the tensioner ring, to maintain tension while loosening or tightening, thus allowing the motor mount to move accordingly without having to get fingers in there and push or pull the motor mount itself. That gets difficult with the printer inside an enclosure.

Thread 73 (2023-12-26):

Twist-to-tension transmission

aamott, 2023-12-26:
Maybe my Ender 3 is an odd one, but the original Z shaft is too short and the pulley hangs off the end of the shaft, resulting in artifacts. In addition, #72 and #51 both point to complexity in the current design. I think it would be simple to redesign the motor mount to use a twist-to-tension design, simplifying the print and eliminating the need for a separate motor carriage and M5 bolt entirely. I used this in [my own printer](https://www.printables.com/model/605726/edit) for the Z axis. I think this would solve the issue with short shafts, bolts, nuts, and remove one more piece of hardware.

Only one screw is anchored. The other 3 move in a path along arcs centered on the anchored screw.

It's not easy to tell, but the Voron Zero has a belted design that uses this: https://www.teamfdm.com/files/file/319-v01-belted-z-drive/

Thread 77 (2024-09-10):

Need some answers for BETA low motor mounted

Gokuh1980, 2024-09-10:
Hi! I made the ultralow version with only one Z motor and it works great, however I have to reprint some parts that didn't turn out quite right. When I went back to the repository I noticed that there is a version with the motor on the bottom and the idlers on top.
I like this approach better because it leaves the weight on the bottom, however I notice that there are two mounts, one with the plate and the adjustment knob and the other to adjust the angle of the motor, which one do you recommend? Is there a reason for the two different versions?

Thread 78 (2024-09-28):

Add recommendation for PC wheels

aamott, 2024-09-28:
Didn't know where to put this, so sorry for that, but it made such a difference with my belted z setup that I had to share.

After something like two years of using this mod, I decided to try PC wheels on the z axis. I'm on the old a4988 drivers, but it looks better than any printer I've ever used before. It's an insane difference switching between PC and Delrin wheels. $3 for the whole upgrade (used the old bearings) but it looks like the work of linear rails. I'd like to recommend a note on PC wheels in the readme because of this.

Jonathan-Ott, 2024-09-29:
Adam, do you have a link to the ones you used?

aamott, 2024-09-30:
Yep! I bought these: [Polycarbonate Xtreme v Mini wheel for Openbuilds](https://www.aliexpress.us/item/3256805539482478.html)

Amazon has some too, though these have bearings preinstalled, no idea of the quality: [Clear Polycarbonate Wheel](https://amzn.to/4ep9UoM)

I had no chance of getting the bearings back out of the polycarbonate wheels without cutting them. Getting them out of the delrin was no problem though once I realized I couldn't push from one side to get them both out. That little plastic lip in the center is obvious in the clear wheels.

Also, in my research, only one person did real tests on the X/Y axes with PC wheels vs delrin and found their first few hours made noticeable dust, just like delrin, but after they wore in it was barely noticeable (again, like delrin). I'll test X and Y later too, since now the rest of the printer is quality enough to see any difference, but may be a little.

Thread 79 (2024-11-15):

bearings that support top rod aren't spinning

Supernovuh, 2024-11-15:
The bearings supporting the top rod are too high friction and acting as bushings rather than bearings. Any advice?

DvaKompota, 2024-11-18:
I'd do the following:
1. Check your printed parts for any deformations, layer shifts, 1-layer problems, etc. to be sure their geometry looks good.
2. Check your rod / lead screw for straightness — roll it on a flat surface with a light behind it and see if there are any gaps along the rod while it rolls.
3. Ease-up/release all the set screws on all 3 gears and try to turn the rod with no load from belts or motor. It should spin with no resistance. If it does, then realign the gears (move the gantry all the way up and down several times) and carefully, watching for any side movement, tighten the set screws on the gears.
4. If nothing helps — order a new rod ($3.65 bucks on [AliExpress](https://www.aliexpress.us/item/3256805641743471.html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)) and/or new bearings and/or reprint the parts

Good luck.

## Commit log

2022-09-19 V3.6 Update
    [1_80TRingGear(Voron).stl, 1_Bearing_Holder.stl, 1_Keybak_MGN_Spacer.stl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]
2022-09-28 Dual Z 80T fix
    [2_80TRingGear(Voron).stl]
2022-09-29 Deleted old BOM and Instructions
2023-02-25 V3.7 update
    [1_80TRingGear(Voron).stl, 1_LeftV3.6.stl, 1_LeftV3.6_Bowden.stl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]
2024-03-05 Bottom-Mounted Update
    [1_Handle_20t.stl, 1_Handle_f623.stl, 1_Motor_Mount_Tensioner_Arm_BottomMount.stl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]
